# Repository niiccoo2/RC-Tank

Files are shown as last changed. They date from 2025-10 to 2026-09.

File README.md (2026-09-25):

Supported by [RTKdata](https://rtkdata.com/)

RTKdata logo



# Ships

_Wondering what a ship is? Watch [this](https://vimeo.com/1111478391) video! Basically, a ship is when you make your project experiancable by others. In this case, that is writing a README about the project and adding some videos so people can see what it is!_

### Version 4 BETA

This is a pretty small version, only 35 hours more than V3. This includes a bit of testing on the old frame, and then the start of designing the new frame. The new frame has been super fun to design but also super hard. Most of this is because all I knew was that I wanted a new frame, nothing else, but also because I didn't really know how to use Fusion. I will say that I learned a lot, and I am ready to finish up the frame. I'm hoping that this is over half of the new frame done, but it might end up taking a lot longer.

Features of new frame worked on for this ship:

- Main body
  - Figuring out how to connect all the aluminum was hard
- Start of the drivetrain

That doesn't sound like a lot, but it really is, especially when you don't know CAD.

CAD file for this ship can be found at `/CAD/V4/ships/V4b/V4b.step`.

**[Bill of materials](./BOM.md)** and **[wiring diagram](./WIRING.md)** — every part needed to build
V4 with quantities, prices and sources (~$2,613 total), and a diagram of how it all wires together.
Frame and drivetrain quantities come straight out of the V4b CAD.

Go look at the build journal (its pretty long! Scroll until you find V4, this ship was on SEP 5): [here!](./JOURNAL.md)

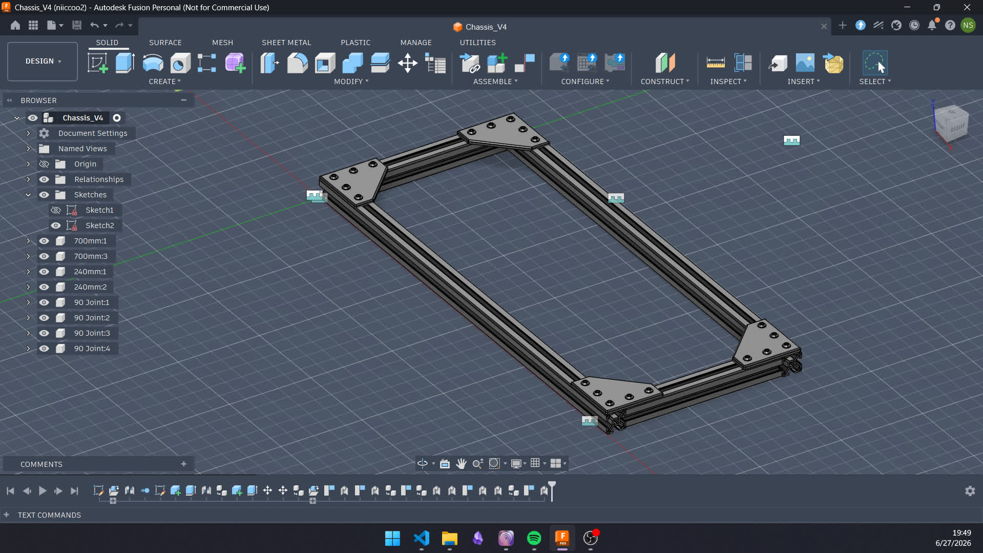
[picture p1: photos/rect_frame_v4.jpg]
Rectangle Frame V4

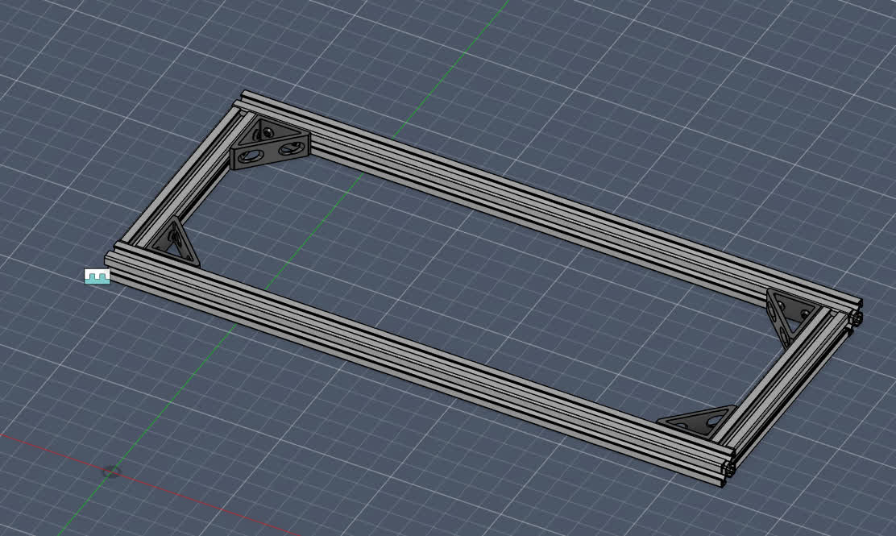
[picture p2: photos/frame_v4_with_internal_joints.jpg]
Chassis V4 with internal joints

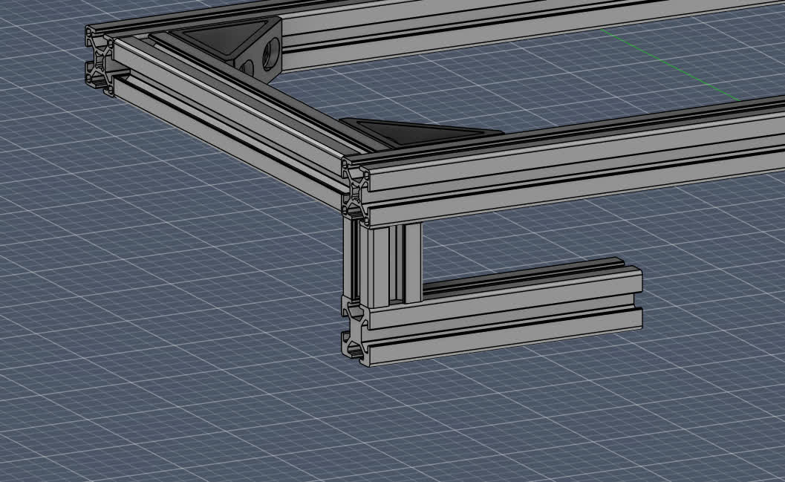
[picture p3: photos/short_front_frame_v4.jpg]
Short front on frame V4

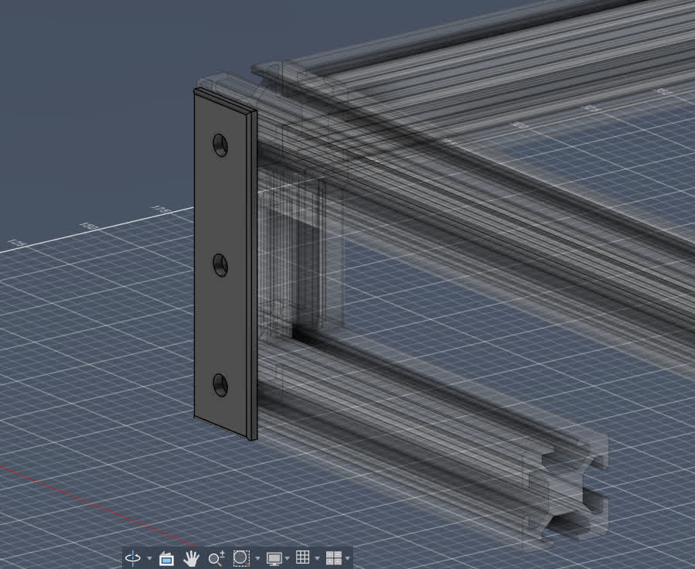
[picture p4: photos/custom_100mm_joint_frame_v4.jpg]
Custom 100mm joint

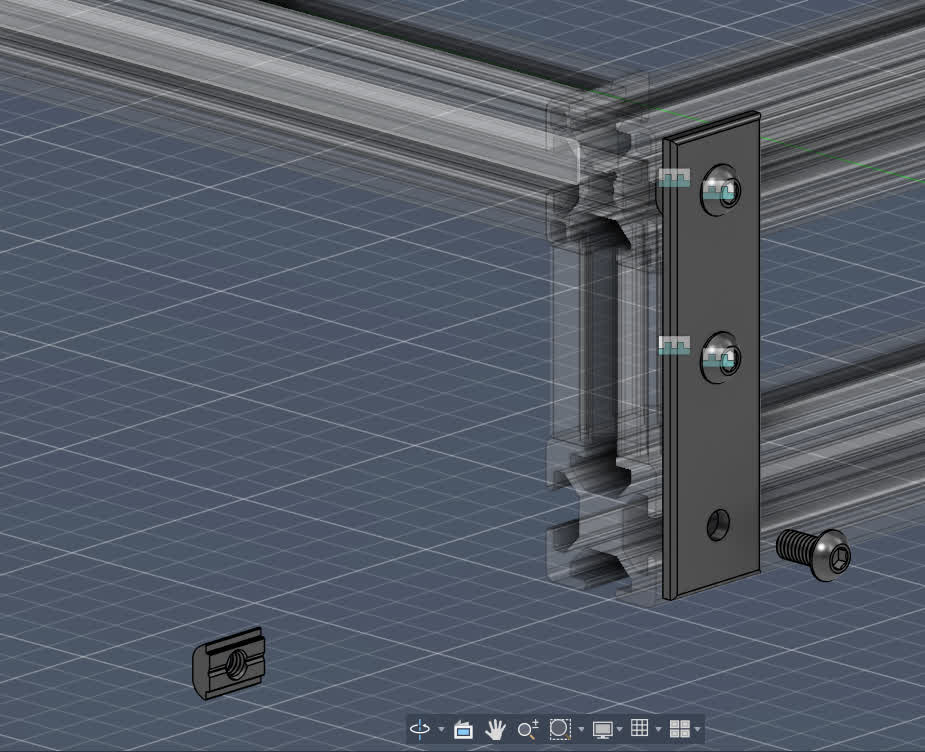
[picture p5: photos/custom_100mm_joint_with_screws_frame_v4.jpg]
Stupid screws

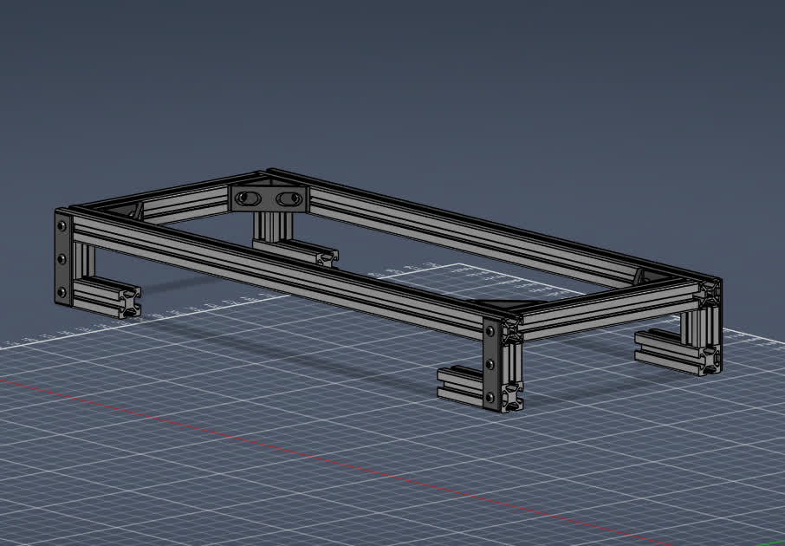
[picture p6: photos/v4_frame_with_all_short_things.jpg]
V4 frame with the short parts now on all sides

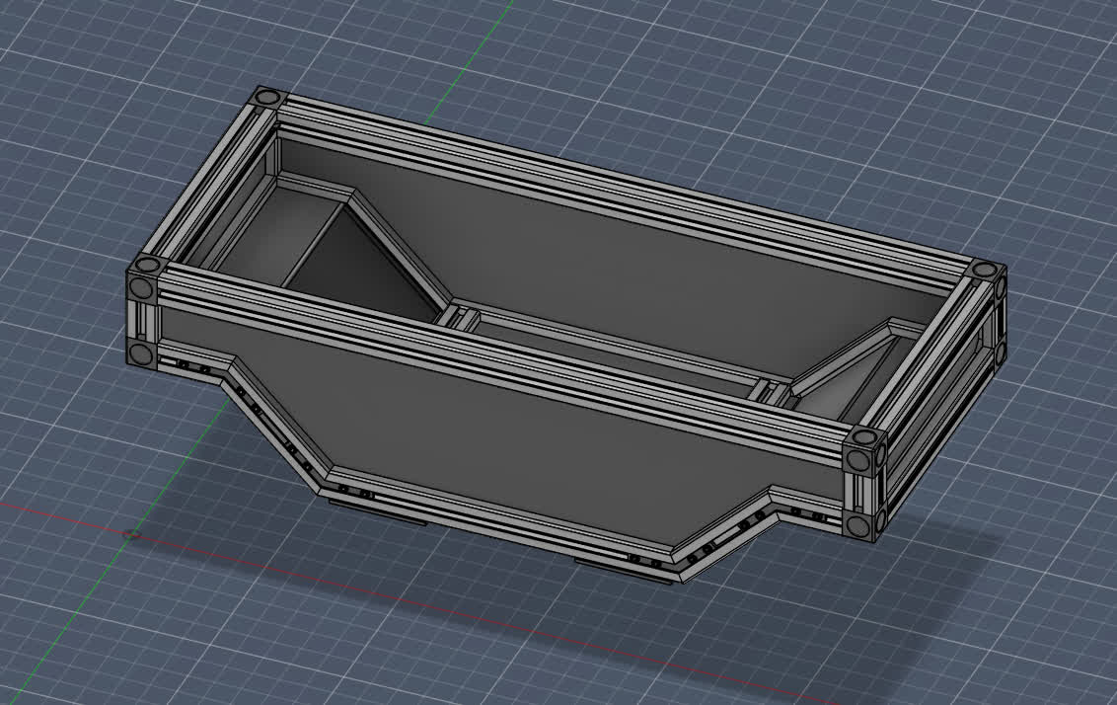
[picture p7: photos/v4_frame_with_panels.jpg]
The new frame with all the panels added

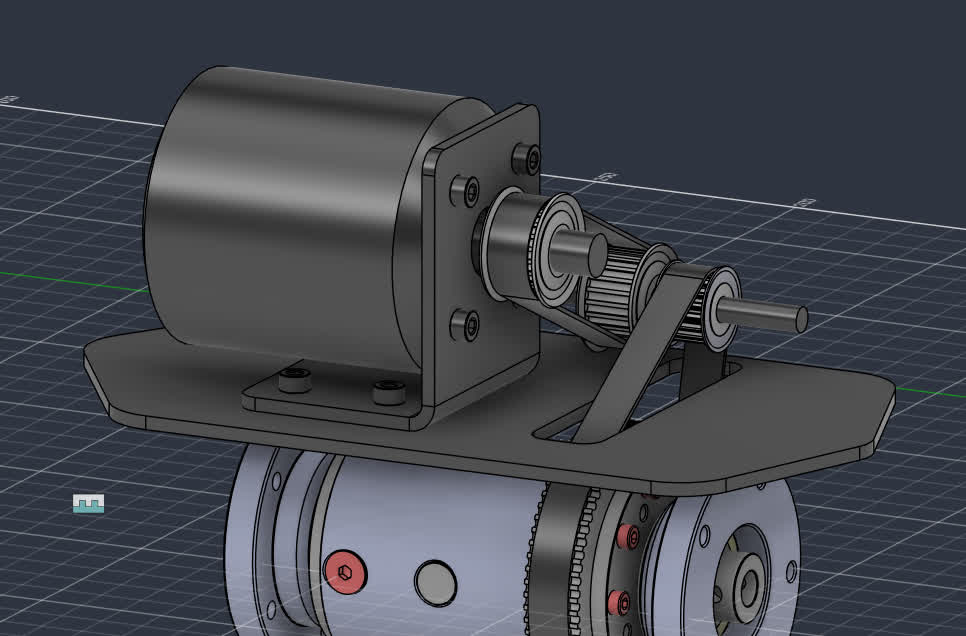
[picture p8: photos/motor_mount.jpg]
Motor mount in question

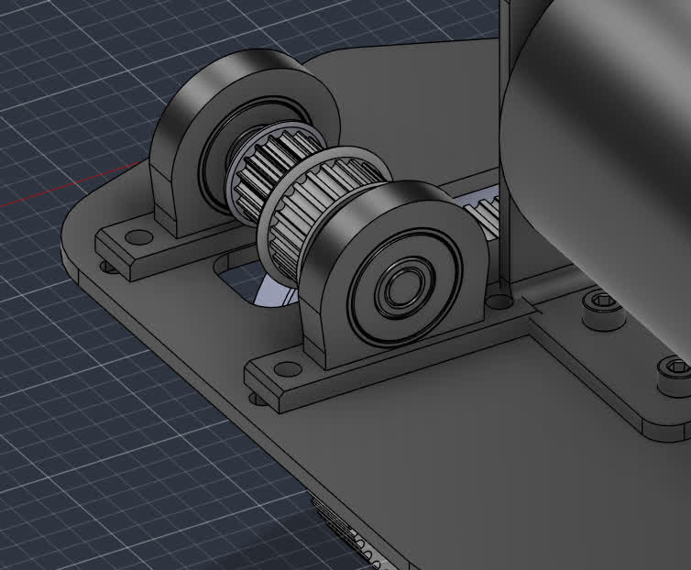
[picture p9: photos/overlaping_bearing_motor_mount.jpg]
The thing overlaping

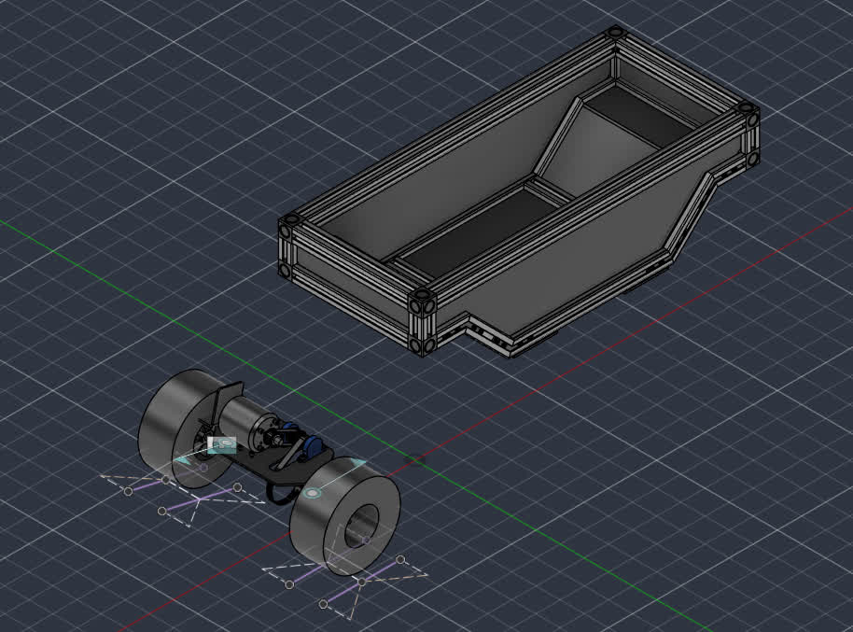
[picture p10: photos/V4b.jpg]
Final V4b


## Version 3

Features:

- Overall:
  - Low latency human driving using cellular
  - Waypoint driving using RTK GPS (under 30mm accuracy)
- Vehicle:
  - Hoverboard motors (very high tourque)
  - Neopixels for headlights and direction lights (red and green)
  - Camera for driving
  - GoPro monuts for videos (not needed to drive, only for extra video)
  - Handles because it weighs 35lbs (around 15kg)
  - Tech specs:
    - Nvidia Jetson Orin Nano
    - SIM7600 cell modem
    - SparkFun GPS-RTK2 Board
    - Hoverboard ECS's
    - 16Ah 4S LiPo battery
- Website:
  - Live video from tank (under 100ms control loop)
  - Live telemetry from tank:
    - Location
    - RTK GPS status
    - Battery voltage
    - Ping
    - Heading
  - Map:
    - View live location of tank
    - Create waypoint routes
    - Send routes to tank
    - Download and upload routes as JSON files
  - Tank settings:
    - Car mode (off lets you control each wheel by itself)
    - Lights
    - FrSky mode (for nicer controlers)
    - Self driving toggle
    - Video toggle
    - Refresh rate setting
  - Go check out the website at [rc.nicosmith.net](https://rc.nicosmith.net)! (Enter anything into text box and click connect)

Version 3 of this project has been based around adding waypoint following capabilities to the tank. There should also be version 3.5 coming out soon which will add ML features, such as staying on sidewalk and avoiding humans. This version has taken a while, but it is well worth it. The project as a whole has taken over 110 hours over 112 days (see, it really is a little bit every day). I redid the entire website UI, redid entire tank-side python software, and added waypoint following code. I have learned a lot about everything, from how much of a pain CSS can be, to how WebRTC doesn't follow system routing priorities, to how people are jerks and will steal stuff. Here are some awesome pictures and videos!

Go look at the build journal (its pretty long): [here!](./JOURNAL.md)

[Videos!](https://drive.proton.me/urls/YN5Q618FJM#a7Ycw6LDcv0I)

Tank in field
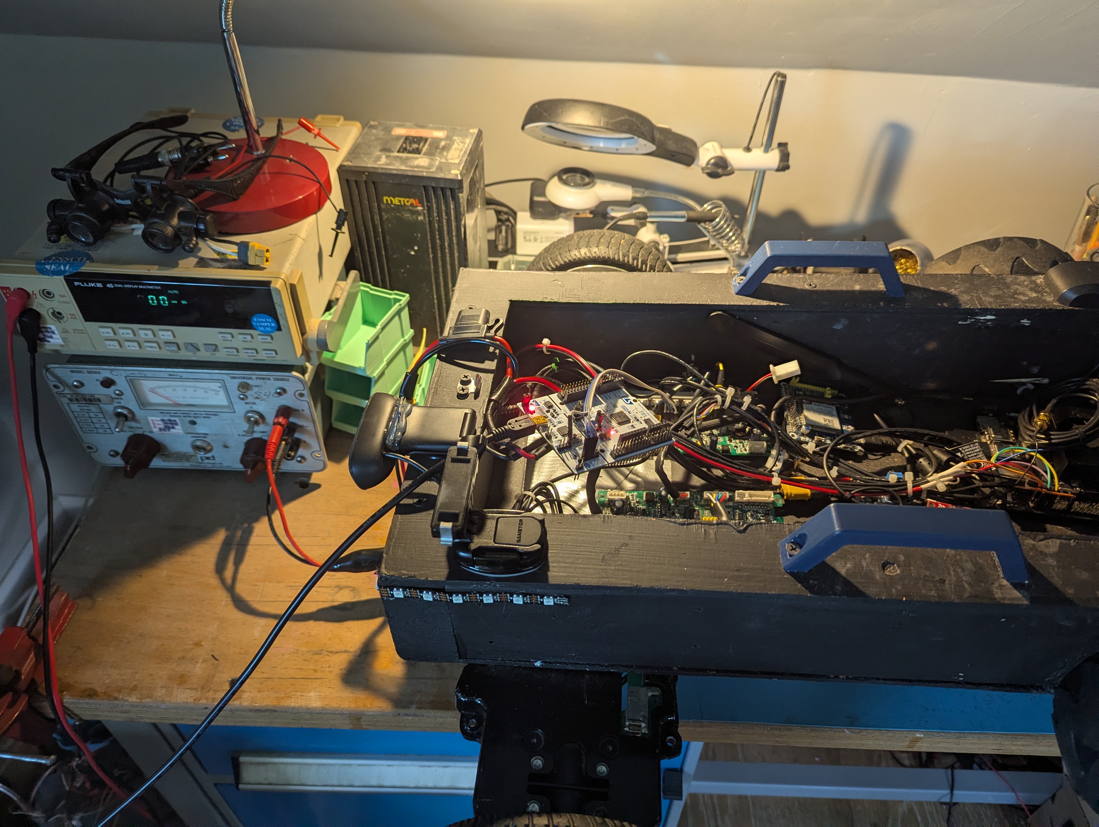
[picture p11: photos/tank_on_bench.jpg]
Tank on workbench

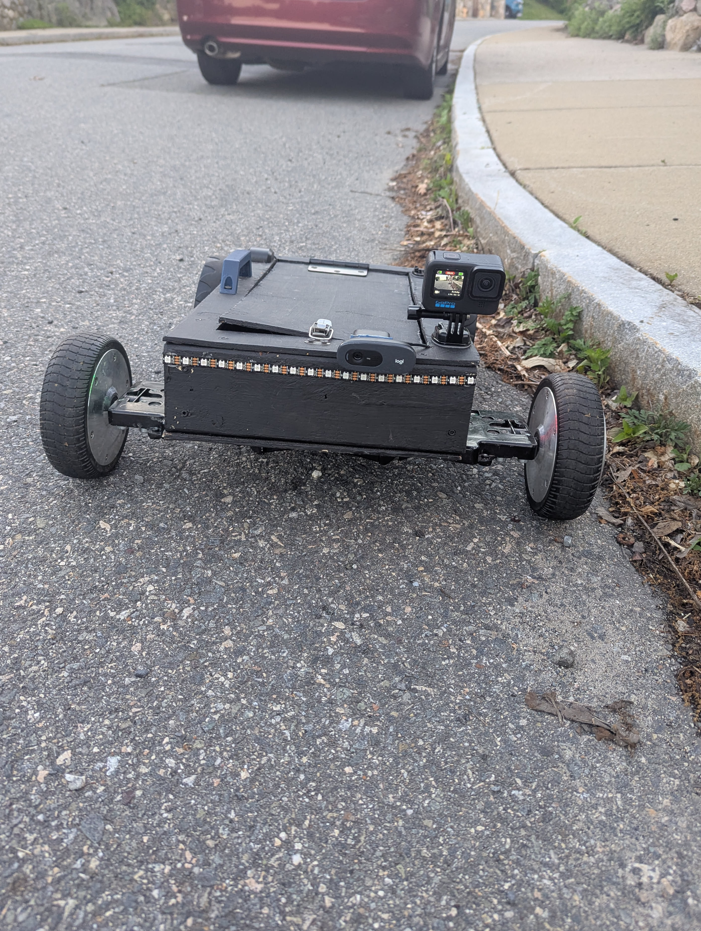
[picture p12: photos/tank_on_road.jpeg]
Tank on road

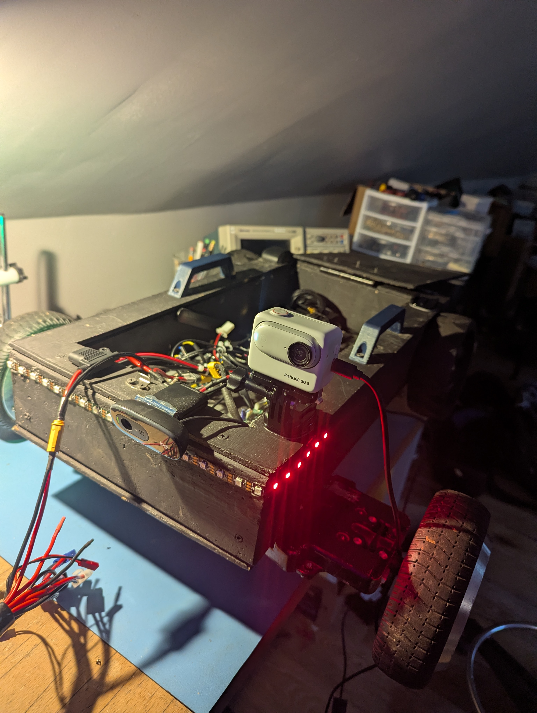
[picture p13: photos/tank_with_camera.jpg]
Tank with camera mounts

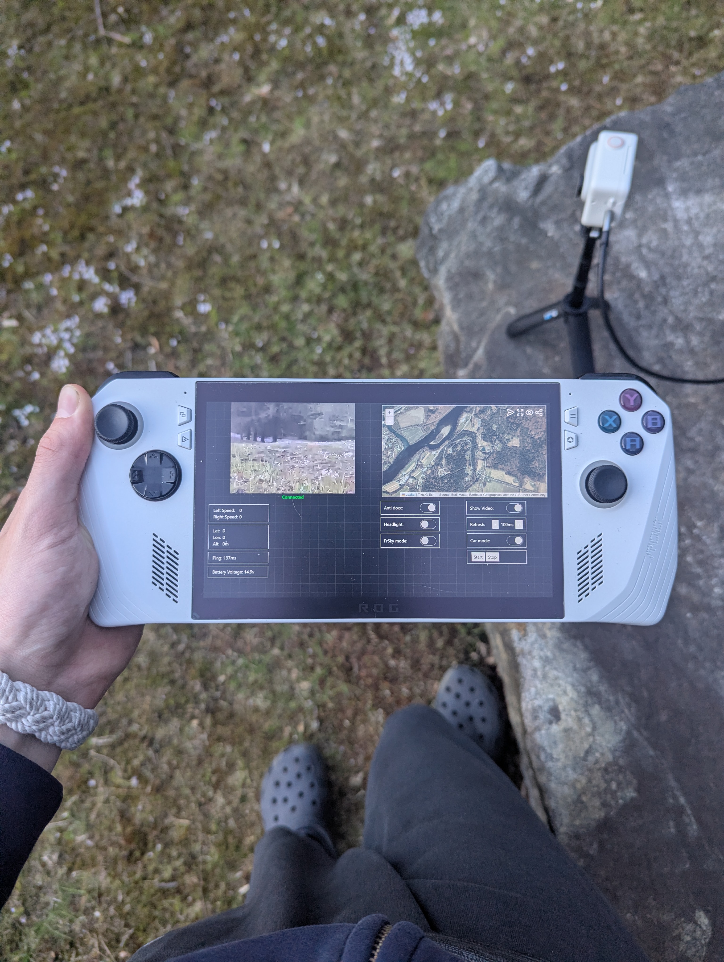
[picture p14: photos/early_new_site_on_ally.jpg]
Early version of new site on ally


## Versions 1 & 2

This is version 2 of my RC-Tank. It is no longer a tank but whatever. I created both versions 1 and 2 for Hack Club [Moonshot](https://moonshot.hackclub.com).

The idea of this project was simple, I had a normal rc car with camera, but it coulden't even go around the block, so I wanted something that would have much better range. Thats where using a cell modem comes in. The main (and big) disadvantage with this is latency, you need < 1.5s or else it becomes very hard to drive. I learned a lot doing this project (not done though!), I spent a lot of time learning about motor contollers and reverse engineering some hoverboard ECS's so I could use the motors I had. The main thing I want to keep working on, is the latency over cell, hopefully I can get webRTC working also. After I have a working human controled rover, then I will use it as the testbed for many more projects such as AI vision control, and GPS waypoints.

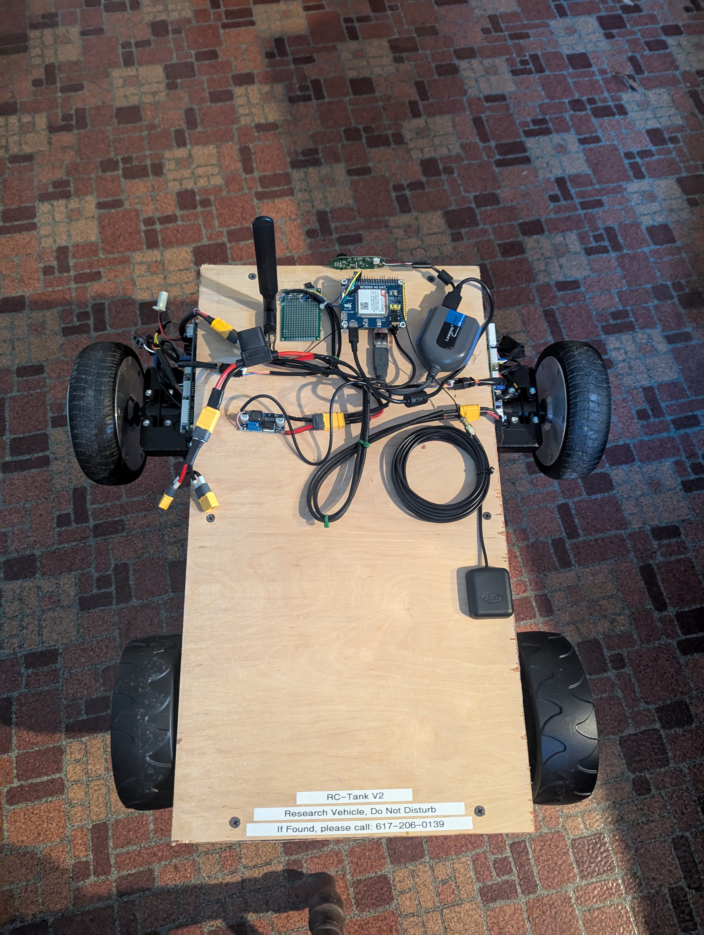
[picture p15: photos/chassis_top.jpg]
Top view of new frame


# Setup

## Internet

### Install Tailscale

Go to [login.tailscale.com/admin/machines](https://login.tailscale.com/admin/machines) and follow instructions for new linux device.

Use this command to start it so ssh will work: `sudo tailscale up --reset --netfilter-mode=off --ssh`.

### Turn off wifi power saving

```shell
sudo iw dev wlP1p1s0 set power_save off
```

You might need to use something like `ifconfig -a` to find the right network interface.

### Add networks and set wifi priority

```shell
sudo nmtui
```

```shell
sudo nmcli c mod "mypreferred" conn.autoconnect-priority 10
```

to set priority; higher number is higher priority.

### Cmd to temp use wifi

```shell
sudo ip route del default via 192.168.1.1 dev wlan0
sudo ip route add default via 192.168.1.1 dev wlan0 metric 50
```

### Cmd to dissconnect from WiFi

```shell
sudo ip link set wlan0 down

sudo ip link set wlan0 up

```

## Jetson specific

### Configure GPIO for SPI

To use SPI on the GPIO pins, you must first run the Jetson-IO python script and enable SPI1 (no idea why you need SPI1 for SPI0).

```shell
sudo /opt/nvidia/jetson-io/jetson-io.py
```

### Resize file system after copying from SD to SSD

```shell
sudo apt install cloud-utils
sudo growpart /dev/nvme0n1 1
sudo resize2fs /dev/nvme0n1p1
```

### Wiring

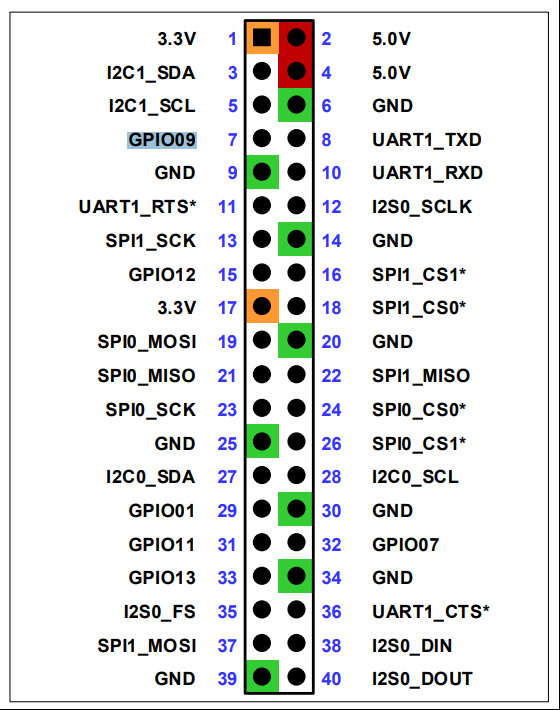
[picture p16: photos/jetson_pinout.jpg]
Jetson Pinout


(Wire color is to just help me)

| Pin # | Purpose  | Item | Wire Color |
| ----- | --- | --- | --- |
| 2 | 5V | Compass Power | Red |
| 3 | I2C1_SDA | Compass Data | Orange |
| 5 | I2C1_SCL | Compass Data | Brown |
| 6 | GND | ESC Serial Ground | Green |
| 8 | UART1_TX | ESC UART RX | Purple |
| 9 | GND | Compass Ground | Black |
| 10 | UART1_RX | ESC UART_TX | Yellow |
| 19 | SPI_0 | Lights Control | Orange |

## Website

You first need to directly go to one of the API endpoints to accept the self signed cert. _Remember that you have to use the :5000 port!_

## Custom TURN / STUN server

`sudo apt install coturn`

`sudo ufw allow 3478/udp`
`sudo ufw allow 3478/tcp`
`sudo ufw allow 50000:50050/udp`

Edit `/etc/turnserver.conf`

```conf
listening-port=3478
listening-ip=<YOUR_PUBLIC_IP>
external-ip=<YOUR_PUBLIC_IP>
realm=rc-tank
user=tank:tankpass
lt-cred-mech
fingerprint

min-port=50000
max-port=50050
```

`sudo systemctl restart coturn`
`sudo systemctl enable coturn`

Set the correct IP inside of `webrtc.py` and `webrtc.ts`

# Running the tank

`sudo JETSON_MODEL_NAME=JETSON_ORIN_NANO python3 ./main.py`

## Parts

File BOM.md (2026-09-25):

# Bill of Materials — V4

Everything needed to build **V4**. V4 is a new vehicle: new frame, new drivetrain, new motors, new
power system. The only things carried over are the compute and sensing stack (Jetson, RTK GPS,
compass, camera, modem, lights), which are listed in section 3.

Quantities for the frame and drivetrain are read straight out of the V4b CAD
(`/CAD/V4/ships/V4b/V4b.step`), so the cut lists and fastener counts are exact.

**Price key:** `~` means estimated. McMaster-Carr doesn't publish prices to search engines, so every
McMaster line is an estimate until I place the order. Prices are USD, no shipping or tax.

Wiring is in [WIRING.md](./WIRING.md).

---

## 1. Frame

All extrusion is **30 mm** T-slot (confirmed by the bracket the CAD uses — McMaster 3136N923 is the
"Flush 90 Degree Angle Bracket for 30mm High Rail"). Cut list from the CAD:

| Item | Qty | Price | Source |
| ---- | --- | ----- | --- |
| 30 mm T-slot extrusion — 700 mm | 2 | — | McMaster-Carr |
| 30 mm T-slot extrusion — 343 mm | 2 | — | McMaster-Carr |
| 30 mm T-slot extrusion — 240 mm | 6 | — | McMaster-Carr |
| 30 mm T-slot extrusion — 141 mm | 4 | — | McMaster-Carr |
| 30 mm T-slot extrusion — 100 mm | 4 | — | McMaster-Carr |
| 30 mm T-slot extrusion — 40 mm | 4 | — | McMaster-Carr |
| ↳ **4.65 m of extrusion**, bought as stock lengths and cut down | — | ~$150 | McMaster-Carr |
| 3-way 90° corner joint | 8 | ~$12 ea = ~$96 | McMaster [5537T864](https://www.mcmaster.com/5537T864/) |
| 45° structural bracket (sloped nose + tail) | 8 | ~$10 ea = ~$80 | McMaster [4844N18](https://www.mcmaster.com/4844N18/) |
| Flush 90° angle bracket, 30 mm rail | 4 | ~$8 ea = ~$32 | McMaster [3136N923](https://www.mcmaster.com/3136N923/) |
| T-slot nuts, screws and washers for all joints | ~120 | ~$50 | McMaster-Carr |
| Aluminum composite sheet, 24" × 60" × 1/8" black | 1 | $71.78 | [Home Depot — Falken ACM-BK-1/8-2460](https://www.homedepot.com/p/Falken-Design-24-in-x-60-in-x-1-8-in-Thick-Aluminum-Composite-ACM-Black-Sheet-Falken-Design-ACM-BK-1-8-2460/308670306) |
| ↳ cut by me into: left side, right side, front short, rear short, bottom | 5 panels | — | from sheet above |
| Front + rear bent panels — laser cut and bent | 2 | ~$90 | SendCutSend |
| Gasket / weatherstrip for the panel seams | 1 | ~$15 | Amazon |
| **Subtotal** | | **~$585** | |

The sheet is 9,120 cm² and the panels need ~3,280 cm², so one sheet covers it with room for mistakes.
Only the two bent panels go to SendCutSend — a plain rectangle was $36 there vs ~$5 of sheet cut at home.

## 2. Drivetrain

Beam axle. One motor per axle, belt down to an idler, second belt to a differential, then U-jointed
rods out to the wheels.

**The V4b CAD contains the front axle only.** The quantities below are for that one axle as modeled.
The full vehicle is 4WD, so double everything (the journal prices 2 diffs, not 1) — that's the
"×2 axles" column.

| Item | Qty / axle | ×2 axles | Price (both axles) | Source |
| ---- | --- | --- | --- | --- |
| Flipsky 6384 190 KV sensored BLDC motor | 1 | 2 | ~$119 ea = ~$238 | [Flipsky](https://flipsky.net/collections/hobby-motors-for-esk8-ebike-efoil) |
| Flipsky VESC (motor controller) | 1 | 2 | ~$80 ea = ~$160 | Flipsky |
| Differential — gears, cross pins, 10×0.2 shims | 1 | 2 | <$100 total | AliExpress, built to [this GrabCAD diff](https://grabcad.com/library/differential-for-rc-quarterscale-cars) scaled up |
| 3D printed diff housing + mounts (PETG) | 1 set | 2 | ~$10 filament | Self-printed |
| HTD 3M 24-tooth pulley, 6 mm bore | 2 | 4 | ~$8 ea = ~$32 | AliExpress |
| HTD 3M belt, 174 mm (motor → idler) | 1 | 2 | ~$6 ea = ~$12 | AliExpress |
| HTD 3M belt (idler → diff) | 1 | 2 | ~$6 ea = ~$12 | AliExpress |
| 440C stainless ball bearing (idler) | 2 | 4 | ~$6 ea = ~$24 | McMaster [4668K235](https://www.mcmaster.com/4668K235/) |
| Idler pulley bearing, p/n 17021800 | 2 | 4 | ~$5 ea = ~$20 | AliExpress |
| 6 mm jack rod (idler shaft) | 1 | 2 | ~$5 ea = ~$10 | McMaster-Carr |
| 8 mm U-joint | 2 | 4 | ~$12 ea = ~$48 | AliExpress |
| 8 mm steel rod — 25 / 34 / 34 / 41 mm cuts | 4 | 8 | ~$15 total | McMaster-Carr |
| 8 mm rod → 12 mm hex wheel adapter | 2 | 4 | ~$10 ea = ~$40 | AliExpress |
| Wheel + tire, 1/5 scale | 2 | 4 | ~$25 ea = ~$100 | AliExpress |
| Mounting plate, motor mount, 2× idler bearing mount — 1/8" (3.2 mm) bent sheet | 1 set | 2 | ~$45 ea = ~$90 | SendCutSend |
| M5 socket head screw, motor to mount | 4 | 8 | ~$10 | McMaster [91292A116](https://www.mcmaster.com/91292A116/) |
| M5 socket head screw, motor mount + idler bolts | 7 | 14 | ~$14 | McMaster [91292A117](https://www.mcmaster.com/91292A117/) |
| Steel hex nut, motor mount | 4 | 8 | ~$5 | McMaster [90592A011](https://www.mcmaster.com/90592A011/) |
| Steel hex nut, idler bolts | 3 | 6 | ~$4 | McMaster [90592A090](https://www.mcmaster.com/90592A090/) |
| Black coated steel washer, motor mount | 4 | 8 | ~$5 | McMaster [93413A211](https://www.mcmaster.com/93413A211/) |
| **Subtotal (both axles)** | | | **~$944** | |

## 3. Power and electronics

The Jetson, GPS, compass, camera, modem and lights move over from V3 unchanged — everything below
the double line is new for V4.

| Item | Qty | Price | Source |
| ---- | --- | ----- | --- |
| 6S LiPo pack — 2 in series gives 12S / 44.4 V | 2 | ~$130 ea = ~$260 | Hobby shop |
| Anti-spark switch + inline fuse (12S) | 1 | ~$25 | Amazon |
| Buck converter, 44.4 V → 5 V | 1 | ~$15 | Amazon |
| XT90 connectors, 10 AWG silicone wire, heat shrink | lot | ~$30 | Amazon |
| — *carried over from V3* — | | | |
| NVIDIA Jetson Orin Nano Super Dev Kit | 1 | $249 paid (now $399) | [NVIDIA](https://www.nvidia.com/en-us/autonomous-machines/embedded-systems/jetson-orin/nano-super-developer-kit/) |
| 512 GB NVMe SSD (boot drive) | 1 | ~$40 | Amazon |
| SparkFun GPS-RTK2 — ZED-F9P (Qwiic) | 1 | $259.95 | [SparkFun GPS-15136](https://www.sparkfun.com/sparkfun-gps-rtk2-board-zed-f9p-qwiic-gps-15136.html) |
| GNSS L1/L2 antenna + SMA cable | 1 | ~$70 | SparkFun |
| Waveshare SIM7600G-H 4G USB dongle + antenna | 1 | ~$70 | [Waveshare](https://www.waveshare.com/sim7600g-h-4g-dongle.htm) |
| LTE SIM + data plan | 1 | ~$10/mo | Carrier |
| Adafruit QMC5883P magnetometer (compass) | 1 | ~$5 | Adafruit |
| USB webcam (driving camera) | 1 | ~$30 | Amazon |
| Powered USB hub | 1 | ~$20 | Amazon |
| WS2812B NeoPixel strip, 30 px | 1 | ~$10 | Amazon |
| **Subtotal** | | **~$1,084** | |

## Totals

| Section | Cost |
| --- | ---- |
| Frame | ~$585 |
| Drivetrain (both axles) | ~$944 |
| Power and electronics | ~$1,084 |
| **Total** | **~$2,613** |

## Not in the V4 build

V1–V3 drove on two hoverboard hub motors and the two GD32 ESC boards out of a salvaged hoverboard,
running [RoboDurden's firmware](https://github.com/RoboDurden/Hoverboard-Firmware-Hack-Gen2.x-GD32).
All of that is replaced in V4 by the Flipsky motors, VESCs and the belt-and-diff drivetrain above.

Tools used but not consumed: 3D printer + PETG, soldering iron, hand tools, drill, calipers, logic
analyzer, ST-Link V2, and Fusion 360 (free hobbyist licence).

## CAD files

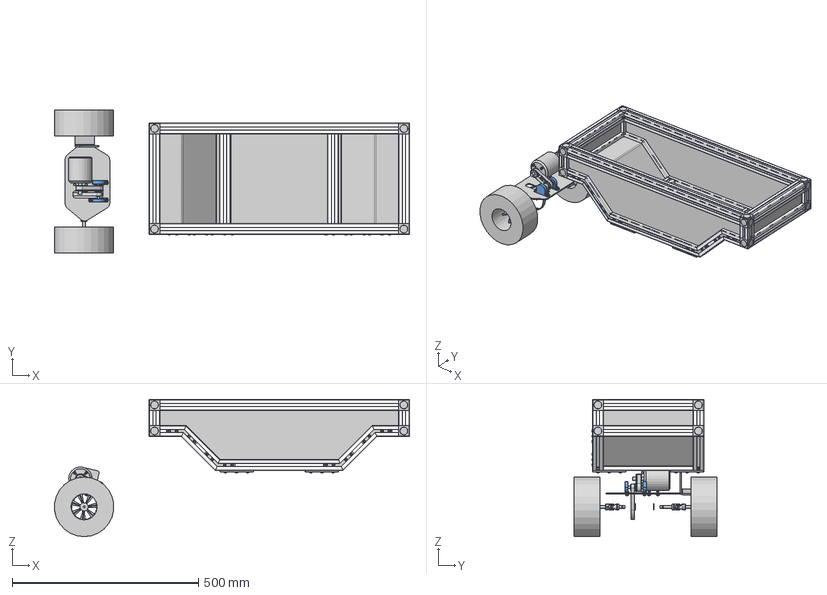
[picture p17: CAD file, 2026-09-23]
CAD/V4/ships/V4b/V4b.step
954.0 x 383.5 x 368.8 mm
4844N18_T-Slotted Framing Structural Bracket x 8
5537T864_T-Slotted Framing x 8
3136N923_Flush 90 Degree Angle Bracket for 30mm High Rail T-Slotted F raming x 4
90592A011_Low-Strength Steel Hex Nuts
93413A211_Black Super-Corrosion-Resistant-Coated Steel Washer
91292A117_18-8 Stainless Steel Socket Head Screw
4668K235_Permanently Lubricated 440C Stainless Steel Ball Bearing x 2
91292A117_18-8 Stainless Steel Socket Head Screw_1 x 2
90592A090_Steel Hex Nut x 2

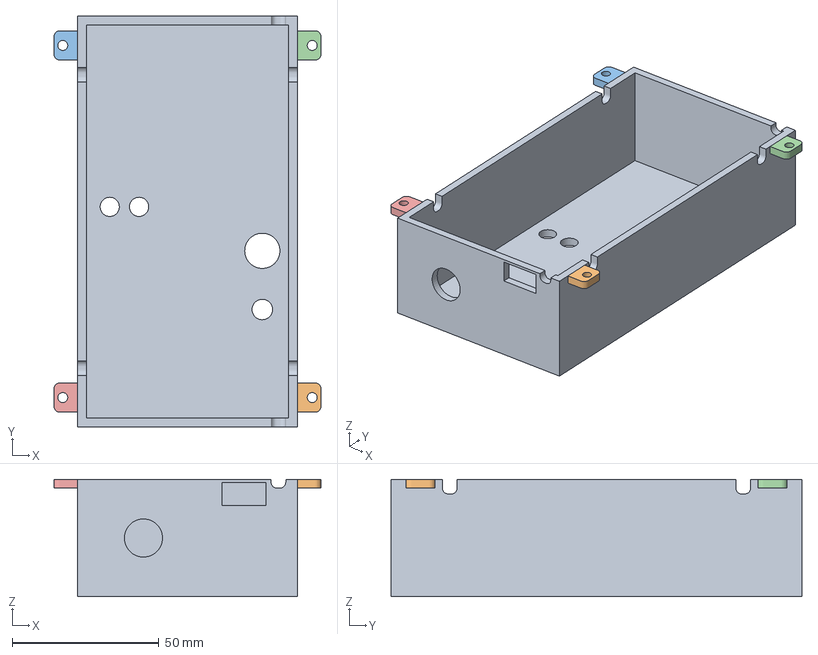
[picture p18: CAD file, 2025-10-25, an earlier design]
CAD/V0.5/cover/Cover_V3.3mf
91.0 x 140.0 x 40.0 mm

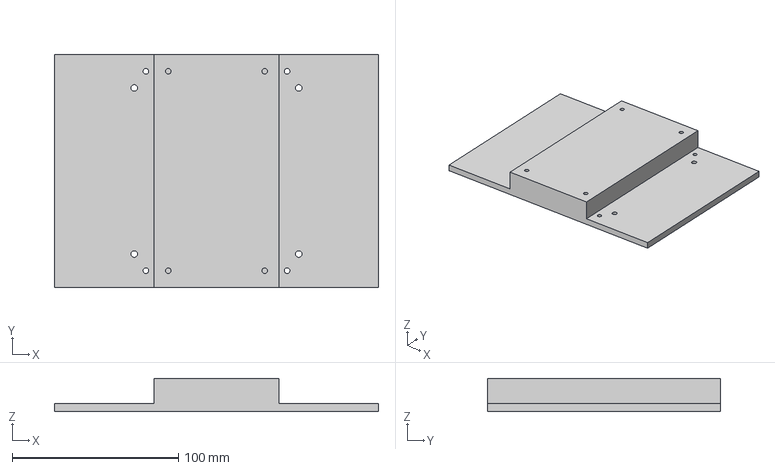
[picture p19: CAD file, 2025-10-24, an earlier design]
CAD/V0.5/riser/Platform_Riser_V4.3mf
195.0 x 140.0 x 20.0 mm

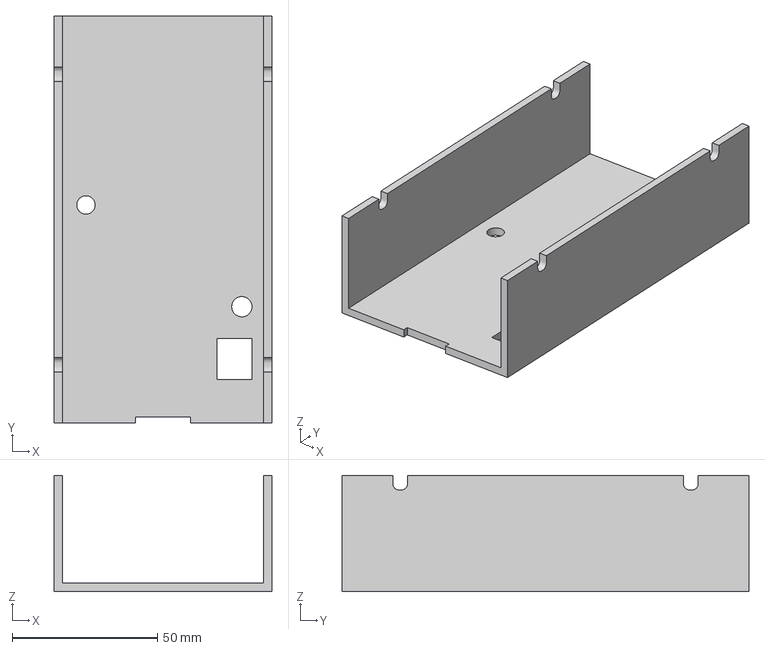
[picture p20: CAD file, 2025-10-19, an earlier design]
CAD/V0.5/cover/Cover_V2.3mf
75.0 x 140.0 x 40.0 mm

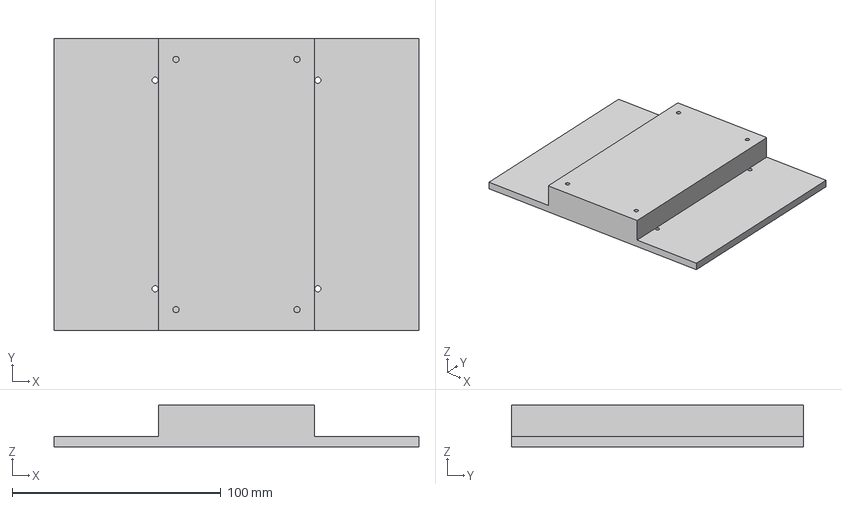
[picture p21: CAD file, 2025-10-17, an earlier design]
CAD/V0.5/riser/Platform_Riser_V3.3mf
175.0 x 140.0 x 20.0 mm

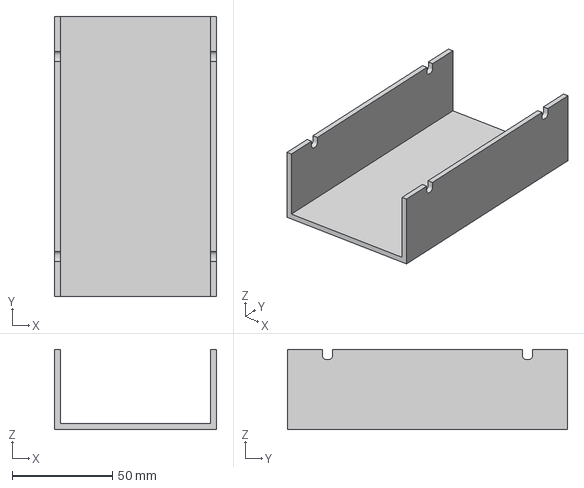
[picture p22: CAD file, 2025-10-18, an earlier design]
CAD/V0.5/cover/Cover.3mf
81.0 x 140.0 x 40.0 mm

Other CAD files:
CAD/V0.5/riser/Platform_Riser_V2.3mf
CAD/V0.5/riser/Platform_Riser.3mf
CAD/V0.5/cover/Cover.f3d
CAD/V0.5/cover/Cover_V2.f3d
CAD/V0.5/cover/Cover_V3.f3d
CAD/V0.5/riser/Platform_Riser.f3d
CAD/V0.5/riser/Platform_Riser_V2.f3d
CAD/V0.5/riser/Platform_Riser_V3.f3d
CAD/V0.5/riser/Platform_Riser_V4.f3d
CAD/V4/Chassis_V4_Rect_Internal_Joints.f3d
CAD/V4/Chassis_V4_Short_On_All_Sides.f3d
CAD/V4/Chassis_V4_Start_On_Front.f3d
CAD/V4/Chassis_V4_with_panels.f3d
CAD/V4/ships/V4b/V4b.3mf

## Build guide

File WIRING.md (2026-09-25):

# Wiring Diagram — V4

How everything in the [BOM](./BOM.md) wires together on **V4**. V4 runs a 12S pack into two VESCs
driving two Flipsky BLDC motors — one per beam axle, belted to a differential. The compute and
sensing side (Jetson, RTK GPS, compass, camera, modem, lights) carries over from V3 unchanged.

Arrows with a voltage are power. Arrows with a protocol are data.

```mermaid
flowchart LR
    subgraph PACK["12S pack"]
        B1["6S LiPo<br>22.2 V"]
        B2["6S LiPo<br>22.2 V"]
    end

    subgraph FRONT["Front axle"]
        VF["Flipsky VESC<br>front"]
        MF["Flipsky 6384<br>190 KV sensored"]
        DF["Belt to idler,<br>belt to diff,<br>U-joints to 2 wheels"]
    end

    subgraph REAR["Rear axle"]
        VR["Flipsky VESC<br>rear"]
        MR["Flipsky 6384<br>190 KV sensored"]
        DR["Belt to idler,<br>belt to diff,<br>U-joints to 2 wheels"]
    end

    B1 -->|series| B2
    B2 -->|44.4 V| FUSE["Fuse +<br>anti-spark switch"]
    FUSE --> BUS["Power bus"]
    BUS -->|44.4 V| VF
    BUS -->|44.4 V| VR
    BUS -->|44.4 V| BUCK["Buck converter<br>44.4 V to 5 V"]

    BUCK -->|5 V| JET
    BUCK -->|5 V| HUB
    BUCK -->|5 V| LED

    VF -->|"3-phase + hall sensor cable"| MF
    VR -->|"3-phase + hall sensor cable"| MR
    MF -->|belts and diff| DF
    MR -->|belts and diff| DR

    JET["Jetson Orin Nano<br>40-pin header"]

    JET -->|"UART1 - pin 8 TX / pin 10 RX / pin 6 GND"| VF
    VF -->|"CAN bus"| VR
    JET -->|"I2C1 - pin 3 SDA / pin 5 SCL<br>pin 2 = 5 V, pin 9 = GND"| CMP["QMC5883P compass"]
    JET -->|"SPI0 - pin 19, 6.4 MHz"| LED["30x WS2812B NeoPixels<br>head / tail / turn"]
    JET -->|USB| HUB["Powered USB hub"]

    HUB -->|USB| CAM["USB camera"]
    HUB -->|"USB - AT / PPP"| MDM["SIM7600G-H 4G modem"]
    HUB -->|"USB - /dev/ttyACM0, 38400"| GPS["SparkFun ZED-F9P<br>RTK GPS"]

    GPS -->|SMA| ANT["GNSS L1/L2 antenna"]
    MDM -->|SMA| LTE["LTE antenna"]

    MDM -->|"internet - RTCM3 in / WebRTC + WS out"| NET(["NTRIP caster<br>+ website"])
```

## Notes

- **The 5 V rail needs its own converter.** The stack pulls ~3.2 A at 5 V (Jetson ~1 A, modem ~2 A,
  camera ~200 mA). On V3 I tried to run it off the ESC BECs, which only gave 1 A each, and it caused
  a long run of bugs that all looked like software problems. Don't repeat that.
- **12S needs an anti-spark switch,** not a bare switch — 44.4 V into the VESC caps will weld a
  plain contact.
- **One VESC is the master.** The Jetson talks UART to the front VESC only; the front VESC forwards
  to the rear over CAN. Same idea as the V3 UART bus, one link from the host instead of two.
- **Motors are sensored,** so each one needs the hall sensor cable back to its VESC as well as the
  three phase wires. Without it low-speed torque is bad, which matters for a heavy rover.
- **SPI must be enabled first** or the lights silently do nothing: run
  `sudo /opt/nvidia/jetson-io/jetson-io.py` and enable SPI1 (yes, SPI1 — it shows up as
  `/dev/spidev0.0`).
- **The compass needs its ground.** It reads garbage rather than erroring if pin 9 is missing.
- **Antennas go outside the shell.** The frame is aluminium, so the GNSS and LTE antennas need SMA
  bulkheads through the top panel.

## Jetson pin assignments

Unchanged from V3, except pins 6/8/10 now go to the front VESC instead of the hoverboard ESC.

| Pin # | Purpose  | Item | Wire Color |
| ----- | --- | --- | --- |
| 2 | 5V | Compass Power | Red |
| 3 | I2C1_SDA | Compass Data | Orange |
| 5 | I2C1_SCL | Compass Data | Brown |
| 6 | GND | VESC Serial Ground | Green |
| 8 | UART1_TX | VESC UART RX | Purple |
| 9 | GND | Compass Ground | Black |
| 10 | UART1_RX | VESC UART TX | Yellow |
| 19 | SPI_0 | Lights Control | Orange |

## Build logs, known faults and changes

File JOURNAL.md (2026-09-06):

# Journal

## **VERSION 1**

I did not count the time building the chassis kit.

### Thursday, October 16th | 30 minutes

Spent 30 minutes designing a simple riser so that I can fit more stuff on the tank. There is not enough room otherwise. This is mainly so I can start installing everything tmrw, once I have an idea of where things fit, I'll make a better version.
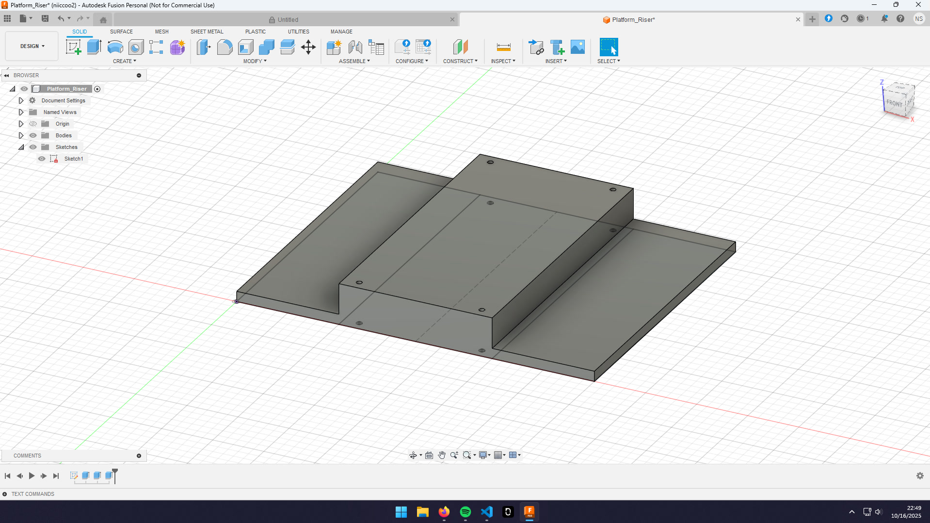
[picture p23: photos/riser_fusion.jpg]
Fusion

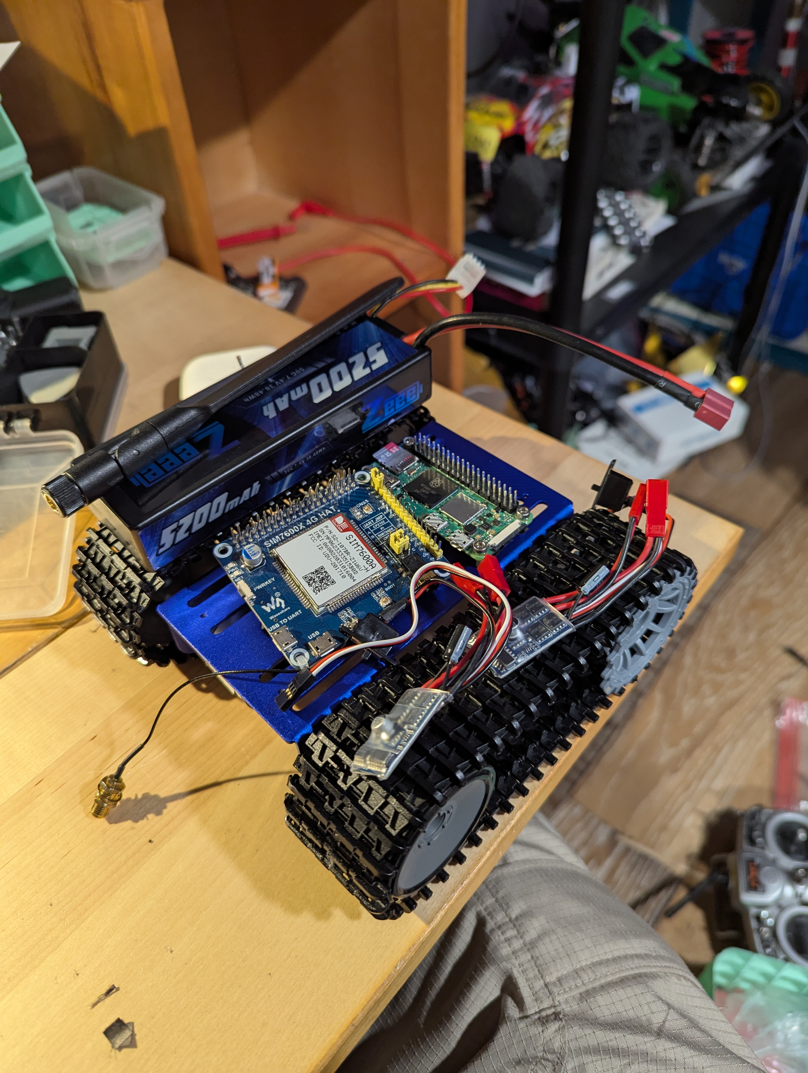
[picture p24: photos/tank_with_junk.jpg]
Wayyy too much stuff on the tank

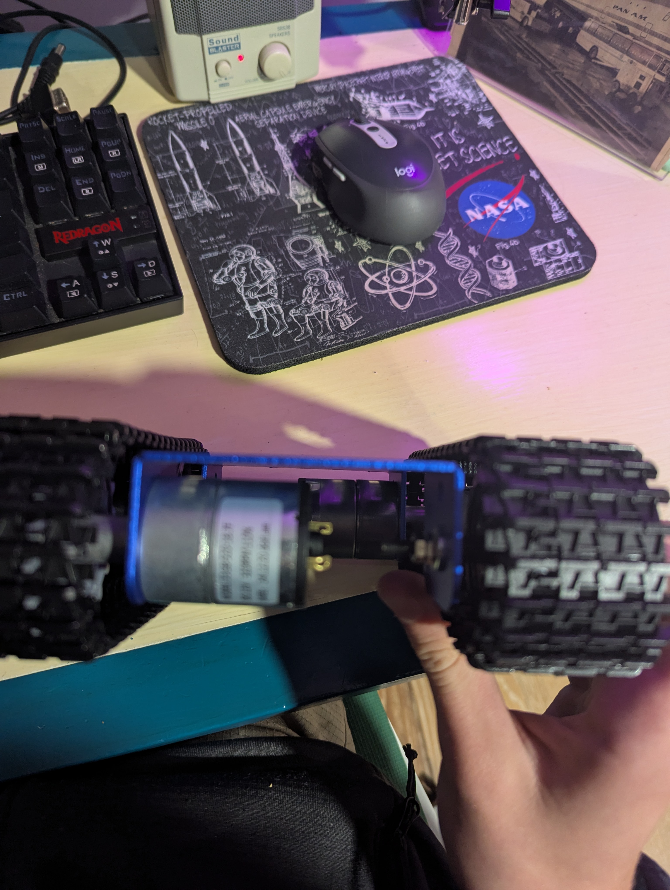
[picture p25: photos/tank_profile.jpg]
Profile of tank


### Friday, October 17th | 4 hours

#### 07:00 | 30 minutes

Tested V1 of the riser. It covered the tracks fine, but I made the screw holes too small and mismeasured where the holes in the chassis are. I spent 30 making V2 with the following improvements.

- Fix size of screw holes
- Fix chassis mountiung hole locations
- Add holes for mounting RPI Zero
- Add holes to ziptie batterys on the edge
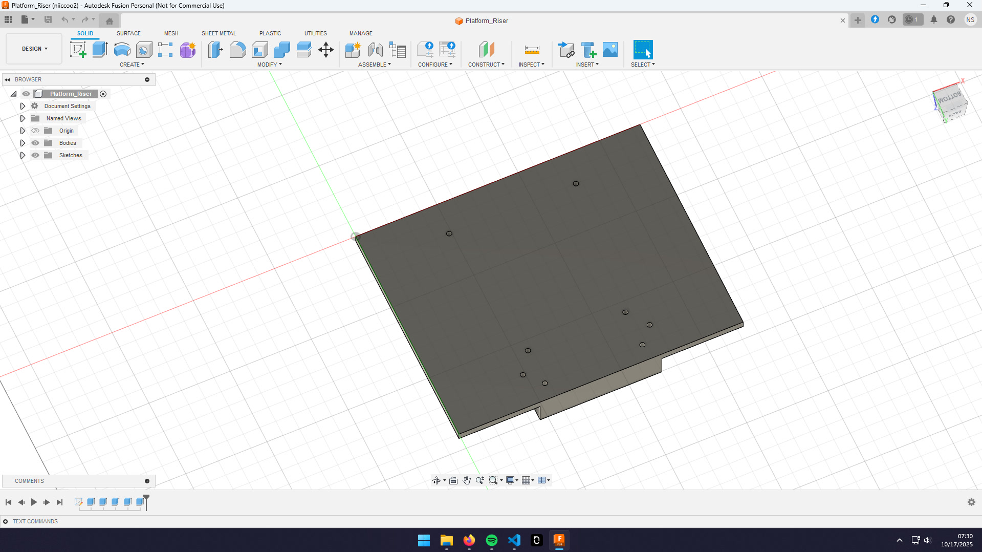
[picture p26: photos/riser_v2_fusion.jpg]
V2 of the riser in fusion
  
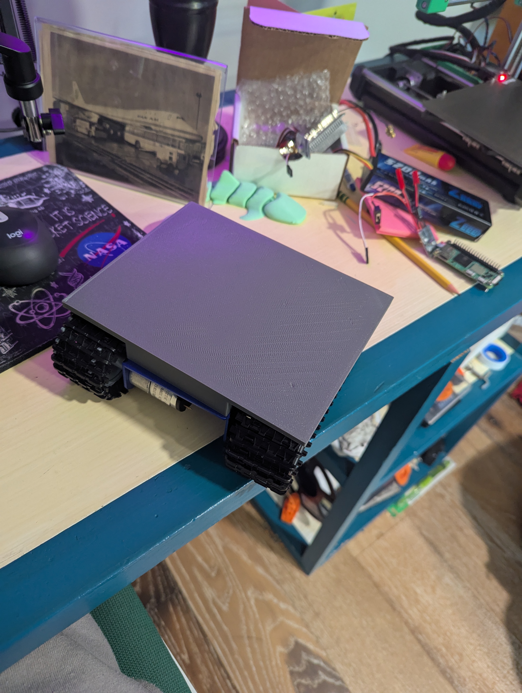
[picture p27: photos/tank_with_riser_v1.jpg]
Tank with V1 of riser
  

#### 16:00 | 30 minutes

Took apart the car and tracks to test V2 of the riser. The mounting holes distance to edge rn is good but apparently I misread the design sheet and made them to far apart. So I made a quick edit and started V3 on the printer.
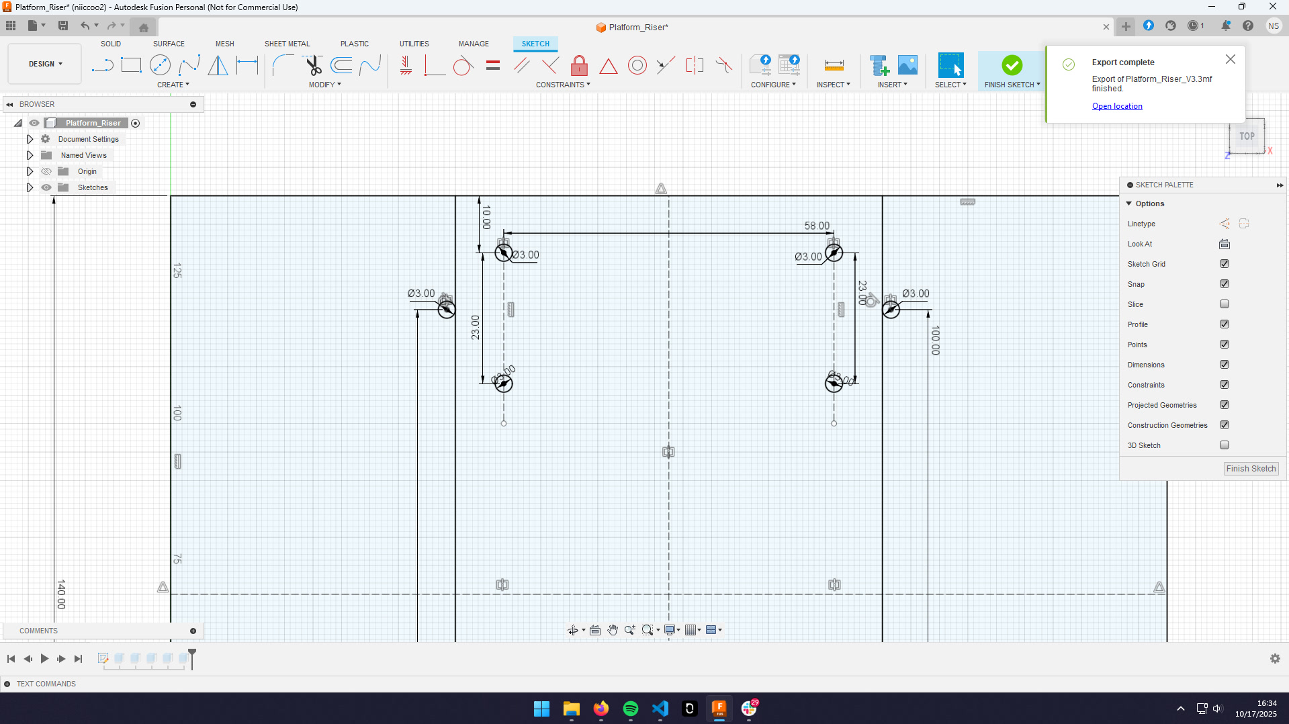
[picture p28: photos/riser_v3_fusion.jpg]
V3 of riser in fusion


#### 18:30 | 1 hour

Soldered a bunch of cables to the motor controllers and did first boot of pi from the tank battery. V3 of the riser is almost done printing. Going to start researching and writing code to make the motors spin!
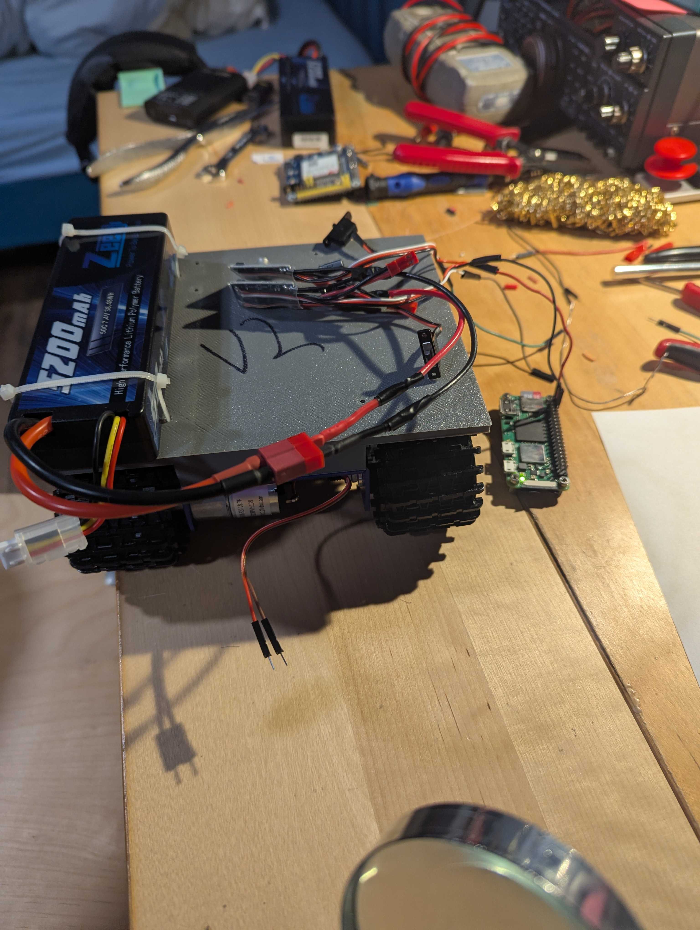
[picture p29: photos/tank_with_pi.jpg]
Tank with pi on it


#### 20:00 | 2 hours

Got the car to drive. But one of the free wheels is locking up, v3 of the riser but finished printing so I'll fix the wheel as I put the new version on. Put V3 of riser on tank. ALL SCREWS LINE UP!!

### Saturday, October 18th | 3.25 hours

#### 10:00 | 1 hour

Added a lcd screen that displays the IP because it kept changing ip. Also wrote code so that it auto displays on boot. Right now its seprate from main.py but at some point I will find a way to intigrate once I feel safe having it auto run main.py.
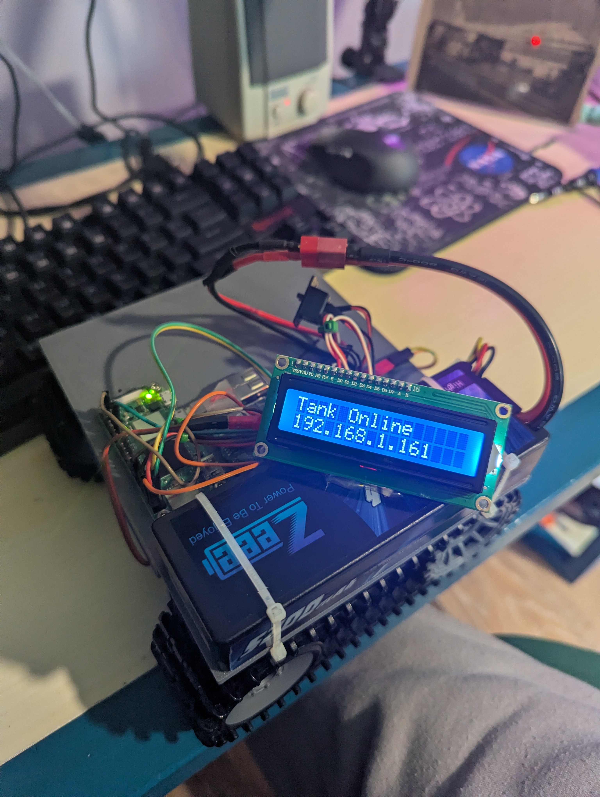
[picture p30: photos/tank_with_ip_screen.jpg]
Tank with screen showing the IP


#### 14:30 | 15 minutes

Seeing how quickly I'm running out of room, I designed a cover for the pi, modem and camera so that I could mount more stuff like the screen, antennas, lights, and other goodies.
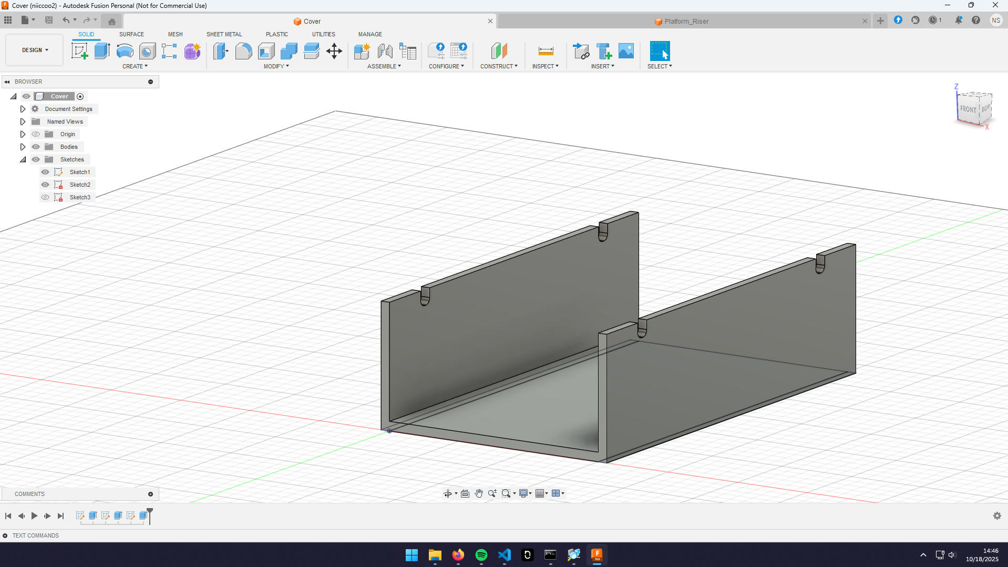
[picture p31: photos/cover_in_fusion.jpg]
Cover in fusion


#### 20:25 | 30 minutes

Tested the cover and made some changes and printed v2. Still going to use hot glue to mount until I redo the riser.
Changes:

- Make total width 75mm instead of 3+75+3
- Add hole for power switches
- Add hole for SMA connector
- Add hole for LCD cables
- Add notch for camera
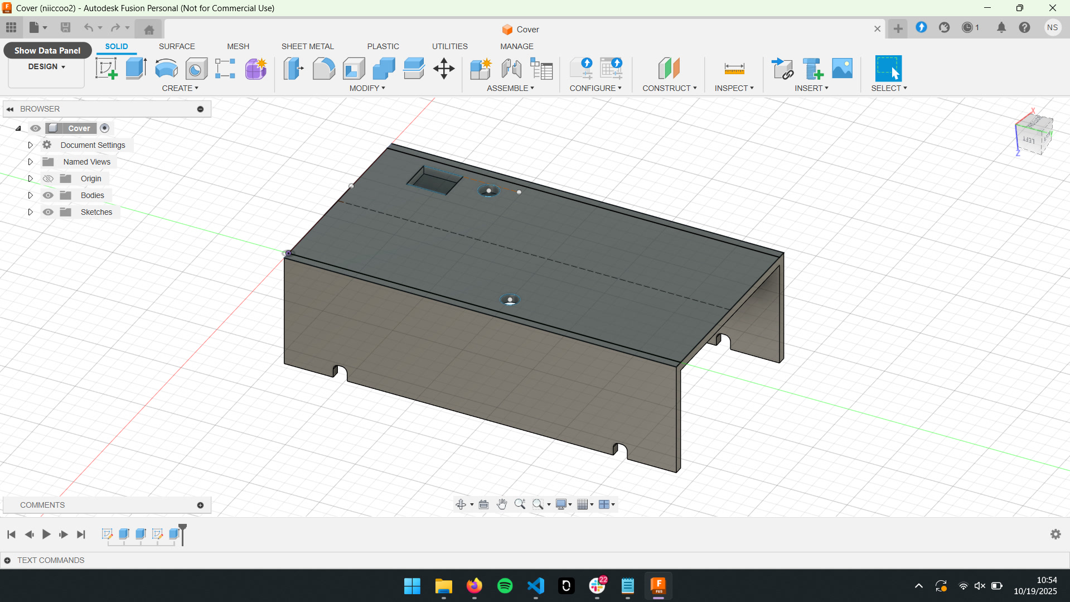
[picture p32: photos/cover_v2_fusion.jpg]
Cover V2 in fusion
  

#### 21:40 | Not logging this time

Just spent 20 minutes figuring out why code was not working, but it was because I was never pulling changes to the tank... Also forgot that a vertical cam makes a vertical stream so going to put it back into original positon and remove the notch in the cover for it. Not a big deal so not printing V3 of cover yet.

#### 22:00 | 1.5 hours

Worked on the website and debugged the twitches. I want to make the website look nicer but I'm going to get some more features working first.
Website changes:

- Embed video stream
- Add connection status
- Add var to enable or disable cam (Added, but did not add a ui switch yet)
- Add ping
- Redo layout

### Sunday, October 19th | 2 hours

#### 08:00 | 30 minutes

Installed the modem and V2 of the cover.
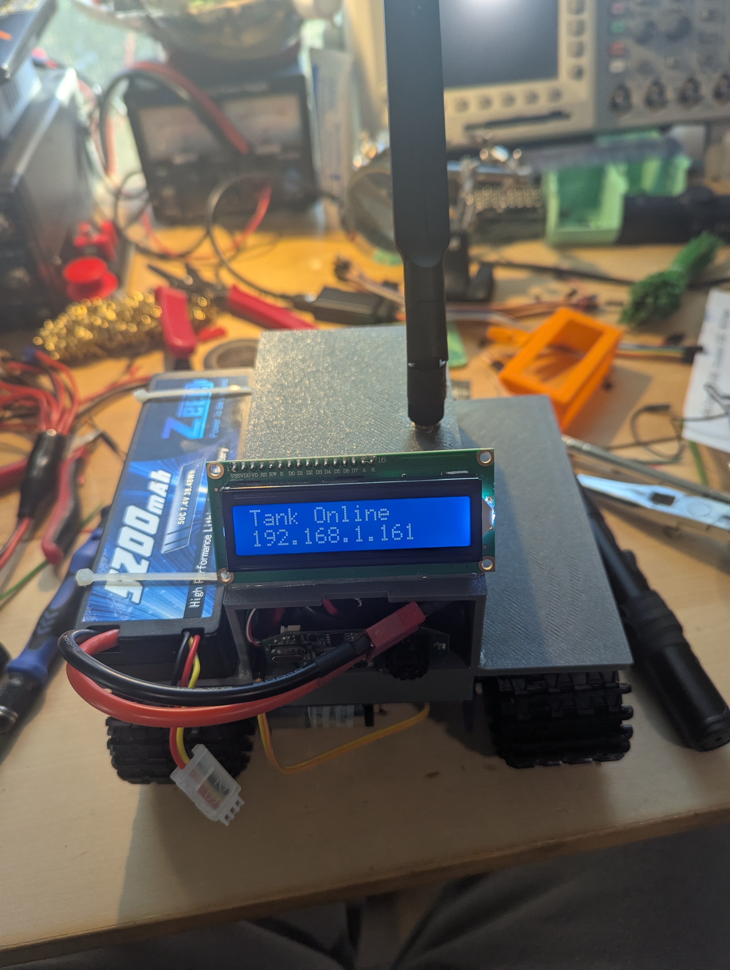
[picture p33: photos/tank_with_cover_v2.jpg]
Cover V2 on tank

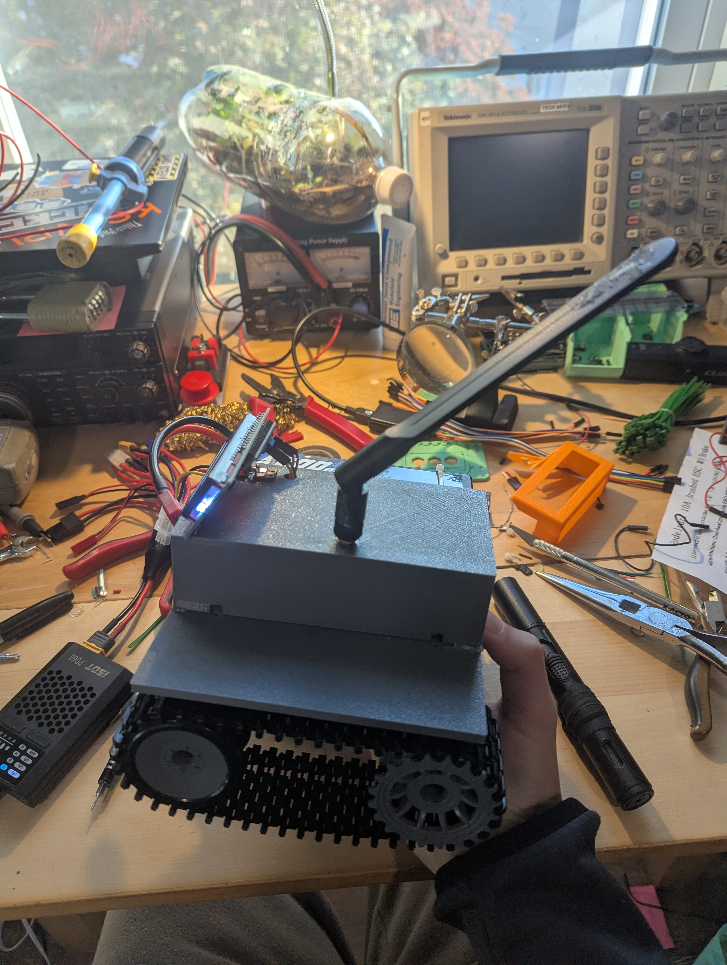
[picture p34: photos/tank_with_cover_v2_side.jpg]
Cover V2 on tank side view


#### 11:00 | 30 minutes

Wrote some quick code that will set the motors to 0 if it has not gotten a cmd in the last 1000ms. To be tested.

#### 20:30 | 30 minutes

Used `sudo nmtui` to set up multiple wifi networks. Then used `nmcli c mod "mypreferred" conn.autoconnect-priority 10` to set priority; higher number is higher priority. The modem has not been set up yet but thats the idea. I'll set up the modem once I have the tank working better on wifi.
| Network Name | Priority |
| --- | --- |
| home1 | 10 |
| home2 | 10 |
| phone | 20 |
| cell modem | 30 |

#### 21:00 | 30 minutes

Spend a bit trying to debug why it is sending tiny bit of power to the motors whenever we read from camera. Seems to be either power related or USB interferince. Tmrw I'll look at the pwm signals to check how they look, as well as calculate the total power everything is drawing and the total the motor contolers can supply from the 5v rail. I think I'm pulling too much so might need a seprate buck converter.

### Monday, October 20th | 30 minutes

#### 07:20 | 30 minutes

Did some research on how much power everything draws. (Everything @ 5v). Each BEC provides 1A so 2A total. A lot of the items did not have stright answers so I'll measure myself at some point. The Pi claims it uses 2.5A but thats crazy so I'll say 1A. Next I'm going to look at the pwm signals to see if there is anything weird about them.
| Device | Power |
| --- | ----- |
| RPI | 1A |
| Modem | 2A |
| Camera | 200mA?|
| LCD | 22mA? |
| Total | 3.2A |

I think all the weird issues are becasue we are drawing too much power from the ESC BEC's. So I'm going to find a better buck comverter to use. In the mean time I'm going to work on the website or something that is not broken.

### Tuesday, October 21st | 1 hour

#### 20:00 | 1 hour

Worked on the website.
Changes:

- Add background
- Fix setting div's
- Add switch for cam on / off (Still working on looks)

### Wendesday, October 22nd | 1 hour

#### 20:00 | 1 hour

Found a buck converter and did some testing to get it ready to be used in the tank. Also started thinking and calculating the correct size fuse to add to the battery.

### Friday, October 24th | 2 hours

#### 17:40 | 30 minutes

Designed V4 of riser. Made the whole thing widers and added holes for the cover to screw into.
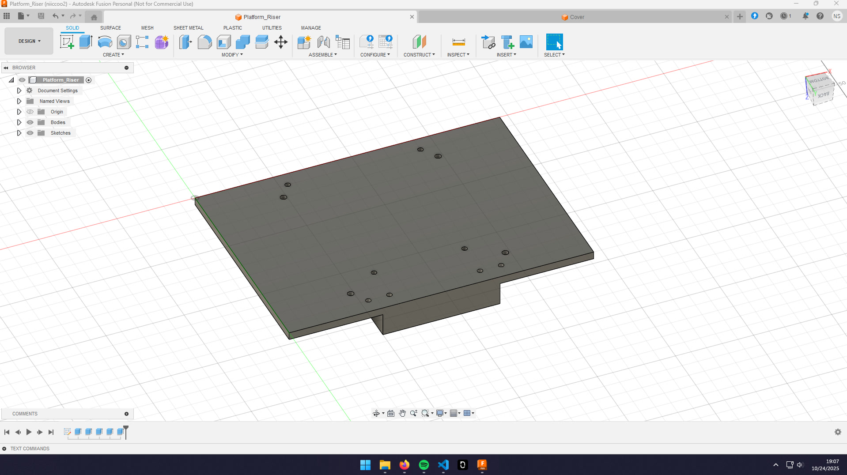
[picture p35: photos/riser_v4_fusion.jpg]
Riser V4 in fusion


### 20:00 | 1.5 hours

Designed V3 of the cover. Main change were the screw holes so I don't need to use hot glue each time I want to mount it. Tmrw morning I'm going to finish some tests on the new buck converter and mount it, along with a fuse and main power switch into the tank. Then mount new cover and see if it fixed anything.
Changes:

- Add hole for GPS SMA connector.
- Add new walls
- Add hole for batt cord
- New hole for new power switch
- GPS and CELL labels
- Screw mounts

### Saturday, October 25th | 1.5 hours

#### 10:00 | 1 hour

Assembled and attached the new riser. I made the holes for the M3 screws a bit too big (3.4mm from 3mm), so that was a mess. Right now you have to take the whole tank apart to replace the riser, not the best, so I might fix that in a new version.

#### 12:00 | 30 minutes

Kept testing the buck converter (forshadowing, it was broken), it was not making sense why the voltage would colapse as soon as a load was added (24 Ohm power resistors).

### Sunday, October 26th | 2 hours

#### 10:00 | 1 hour

Found out that the buck converter I was trying to use was damaged. After I found that out and got some new ones, everything was making much more sense. The converter was able to buck a 6v input to 5v out. That is better than the specs but thats good. It was also able to power some 24 Ohm power resistors. I=V/R 5/24=0.204 ish Amps.

#### 22:00 | 1 hour

Soldered the new buck converter, fuse, and power switch into the tank. Now I need to fit this mess into the new cover I printed... After being powered on for a few secs, something starts making a weird noise, I'll look into it in the morning.

### Wendsday, October 29th | 1.30 hours

#### 20:00 | 1.30 hours

Finished making the main page look nice. Also made the IP picker screen, so when you open the site, you can just type the current ip instead of editing code. Now have to figure out why the camera is not streaming.

### Thursday, October 30th | 2.5 hours

#### 06:40 | 1 hour

Finaly put the cover on the tank, it involved a lot of pushing hard, so I'll make the next version of the cover much taller. I also need to make all the m3 screw holes smaller. And need to space the cell and GPS connectors apart more. It looks likes it's powering on but never connects to tailscale so I'll fix all of this after school.
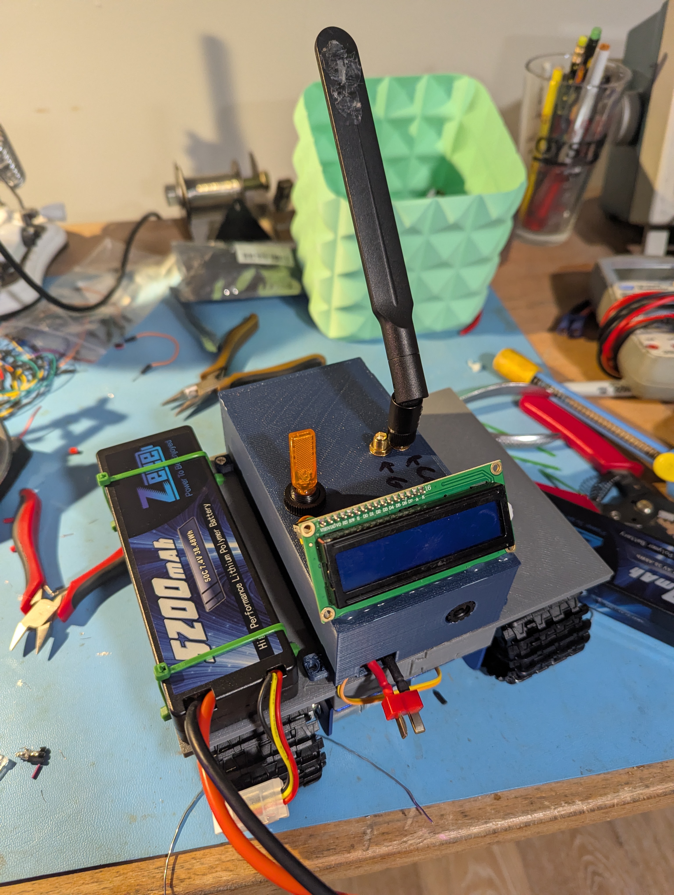
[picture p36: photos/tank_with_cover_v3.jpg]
Tank with cover V3


#### 21:00 | 0.3 hours

Figured out why the tank is not working... I may have snaped the SD card. Just reflashed a card an now am going to set everything up again.
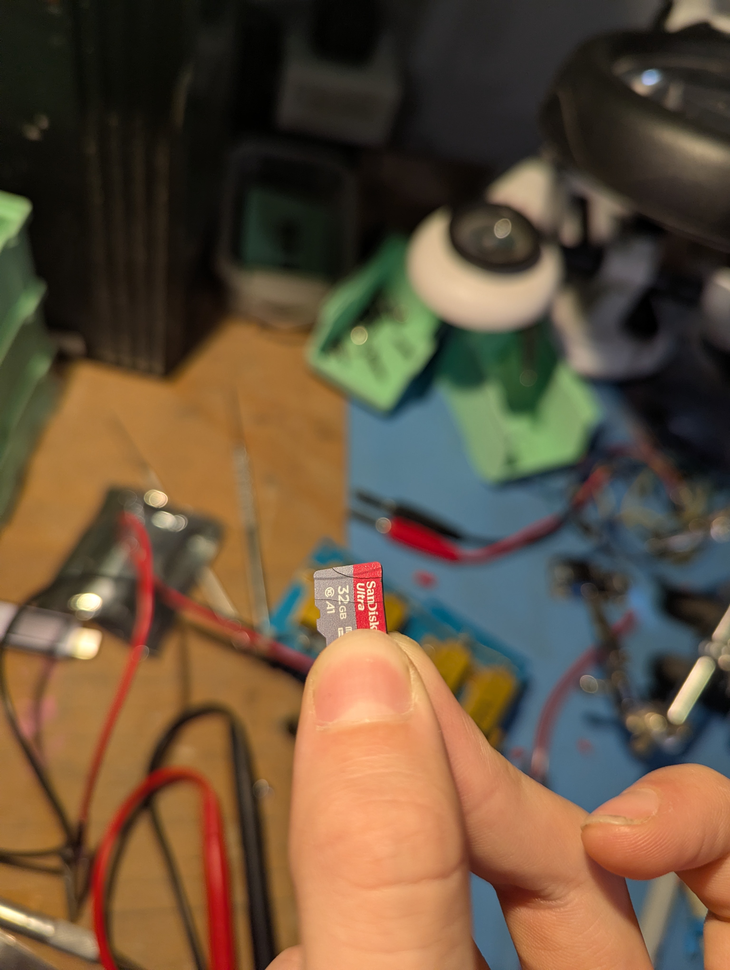
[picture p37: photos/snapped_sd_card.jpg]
Snapped SD card


#### 21:30 | 1 hour

Set everything up on the pi. Also wrote some instructions for setup to help me and or others next time. Debugged some issues with the website, need to make it only try to run any of the functions that use ip once the ip is set. It's also really laggy, but I'll fix that in the morning.

#### 22:30 | 0.2 hours

~~Site seems to not work when hosted on vercel, only works on localhost. This is probably due to the fact that its trying to call the API requests from the backend, not the client.~~ I think that was just becasue the site was not working in general... Anyways, fixed the site, so now you can enter the IP and it actually tries to connect.

### Saturday, November 1st | 3.5 Hours

#### 12:00 | 1.5 hours

Did some debugging. Got the timeout feature working. Also changed the amount the website sends motor cmds from every 10ms to every 100ms. That helped with the lag a lot. Added a thing on website to change that value.

#### 15:00 | 2 hours

Wrote code to let you control the tank like a car, also added switch to turn that on and off. Refactored the whole python file to use classes. Got a bit of help from AI to reduce video bandwidth. It now looks rlly bad, and feels the same on latency, but the bandwidth is down by A LOT.

### Sunday, November 2nd | 3 hours

#### 10:00 | 2 hours

Spent forever trying to get ppp (network over serial) working on the modem. The modem itself will get an IP from the cell towers, but once I start asking for a ppp address, I get ghosted. I had the same issue with this modem on my last project, and I was naive to think it would work better this time. The solution is to use usb, but I'm already using the one usb port for the camera, so I'll have to wire up a hub.

#### 15:00 | 1 hour

Tested the car on it's first long range test. It uhh worked. But the latency was annoying, a lot of the time it was usable, but with color off I coulden't tell the difference between the road and dirt, so I turned on color, that broke everything. I hope it works better once I'm back in Boston, but I don't want to get my hopes up too much. Another issue is not a bug, but once your on the road, it feels SUPER slow. It's fine in a house but once you are on the street its wayyy too slow. So I'm going to start designing a new chassis made out of aluminum extrutions, with a higher speed and more room for goodies.

New things for v2:

- Bigger chassis
- Switch to electon so we can use the hosts serial ports for radios and such
- Faster top speed

### Monday, November 3rd | .5 hours

#### 17:30 | 0.5 hours

Tested the tank in Boston (hopefully has faster cell). It worked, but has a lot to be wanted... It was night so I could bearly see what I was doing. [filz.cc/f/UVyD.mp4](https://filz.cc/f/UVyD.mp4) [filz.cc/f/diph.mp4](https://filz.cc/f/diph.mp4)
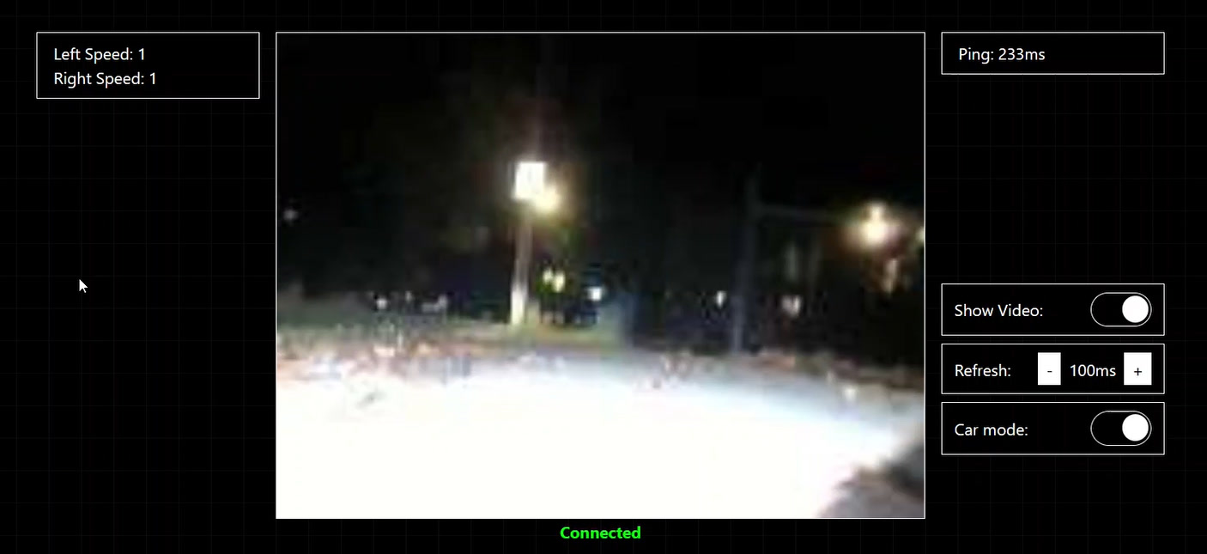
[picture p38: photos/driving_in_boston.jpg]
Driving in Boston


## **VERSION 2**

### Tuesday, November 4th | 1.5 hours

#### 17:00 | 1 hour

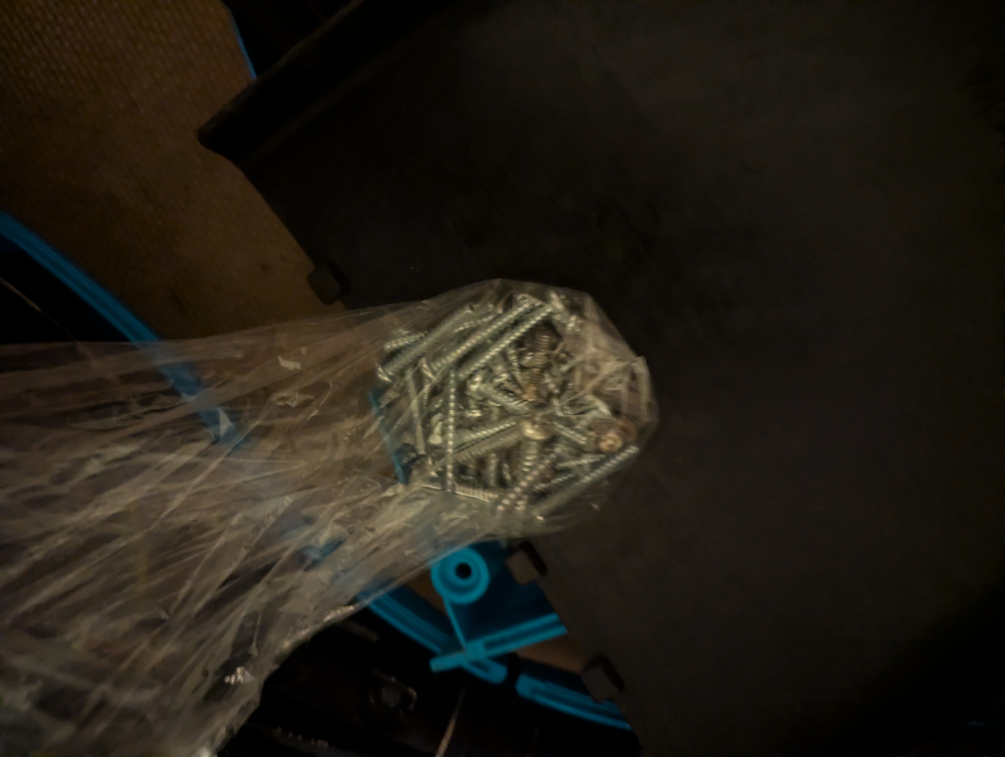
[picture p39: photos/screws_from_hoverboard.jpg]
Wayyyy too many screws
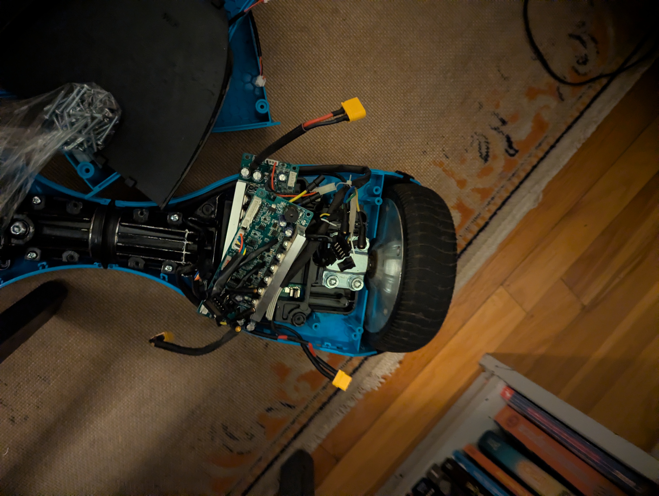
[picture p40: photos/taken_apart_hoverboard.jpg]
Taken apart hoverboard
Started by checking btop (better htop) to see cpu usage while running the script. THe cpu is around 10% when running, so we don't need a faster pi. Then I took apart a hover board to get to the brushless motors, this is going to be the main motors for V2 until I feel I need better ones.  

#### 20:00 | 0.5 hours

Started thinking about how to design the robot and doing the cad. Right now I'm stuck on the suspension because I rally have to build around it. CAD is hard :/

### Wednesday, November 5th | 1.5 hours

#### 07:30 | 0.5 hours

Started reading about WebRTC and how to use it, seems helpful due too variable bitrate among other features. Just built out more in general. To use this libary I found, it looks like I need to switch to FastAPI so I started doing that. Later today I'm going to build the frame for the bigger chassis. It's going to be really simple to start, just a rectangle, but it will be much bigger and allow me to start getting the motors working.

#### 21:00 | 1 hour

Found this repo that looks good, it will let me use the motor contolers already in the hoverboard mobo. I might make the robot in to a hoverboard for now so I don't need to get more parts, depends on if the repo will do the balance, if not, I'll jsut use the motors and mobo. I'll look into a bit more in the morning and figure out my next steps for hardware. [Repo Link](https://github.com/RoboDurden/Hoverboard-Firmware-Hack-Gen2.x-GD32)

### Thursday, November 6th | 2.5 hours

#### 07:00 | 0.5 hours

Wired up this ESP8266 to flash the new firmware to the hoverboard boards. Also got headers ready for the boards. Now i just need to solder the headers and flash it, but the pins for flashing are a weird size so the headers don't want to solder.

#### 17:00 | 1 hour

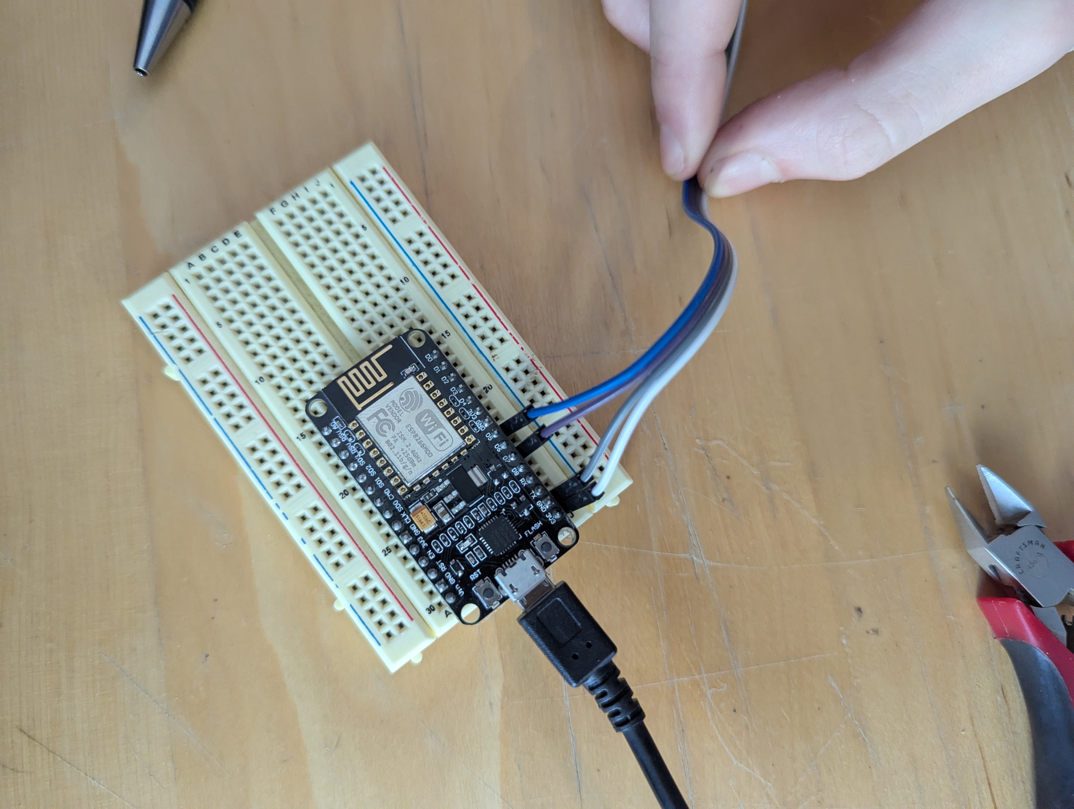
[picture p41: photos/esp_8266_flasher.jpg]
ESP8266 I'm using to flash the hoverboard
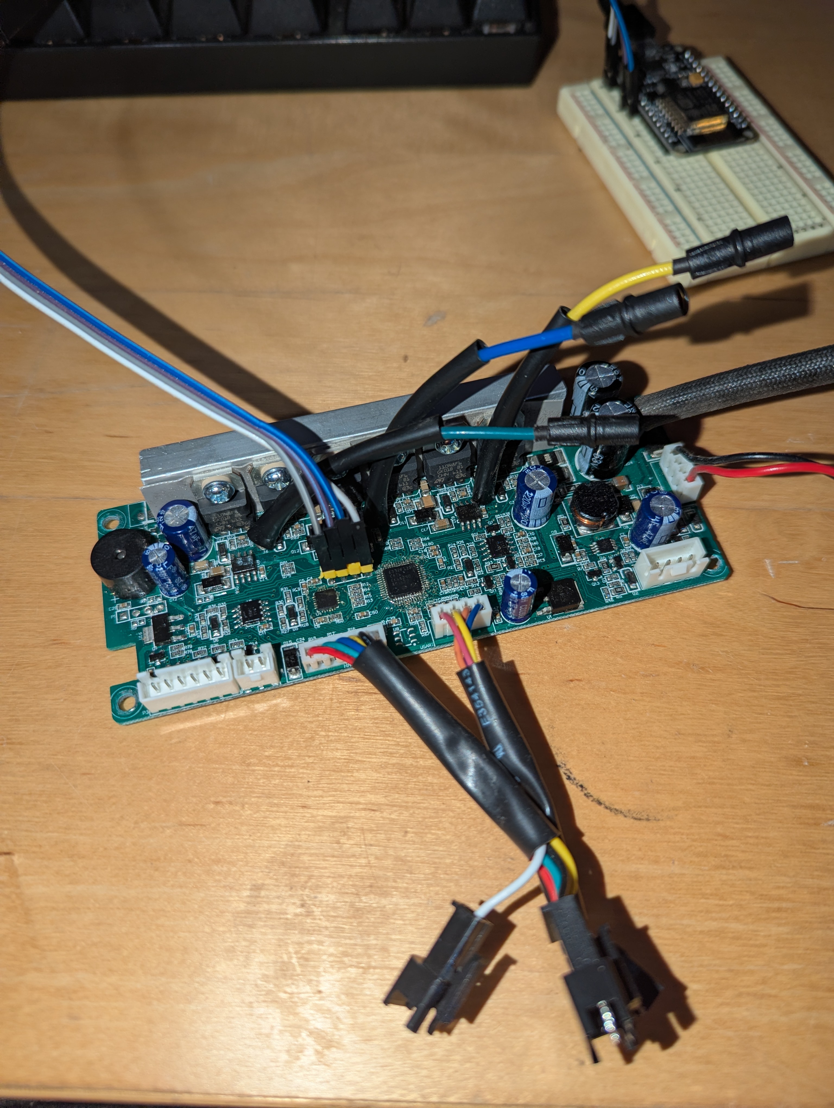
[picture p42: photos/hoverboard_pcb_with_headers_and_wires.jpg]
Hoverboard PCB with nice headers I added
Soldered headers to the hoverboard PCB's to flash. Now I'm trying to follow the **not very helpful** guide in the repo on how to set up the flasher and all that. I have about 20 programs open rn and bearly know what half of them do...  

#### 21:30 | 1 hour

Set up Keil and some other apps to try and program it. I'm making no progress though. I think I'm going to try and use a rpi pico instead of ESP8266 and start over tmrw.

### Friday, November 7th | 2 hours

#### 20:30 | 1 hour

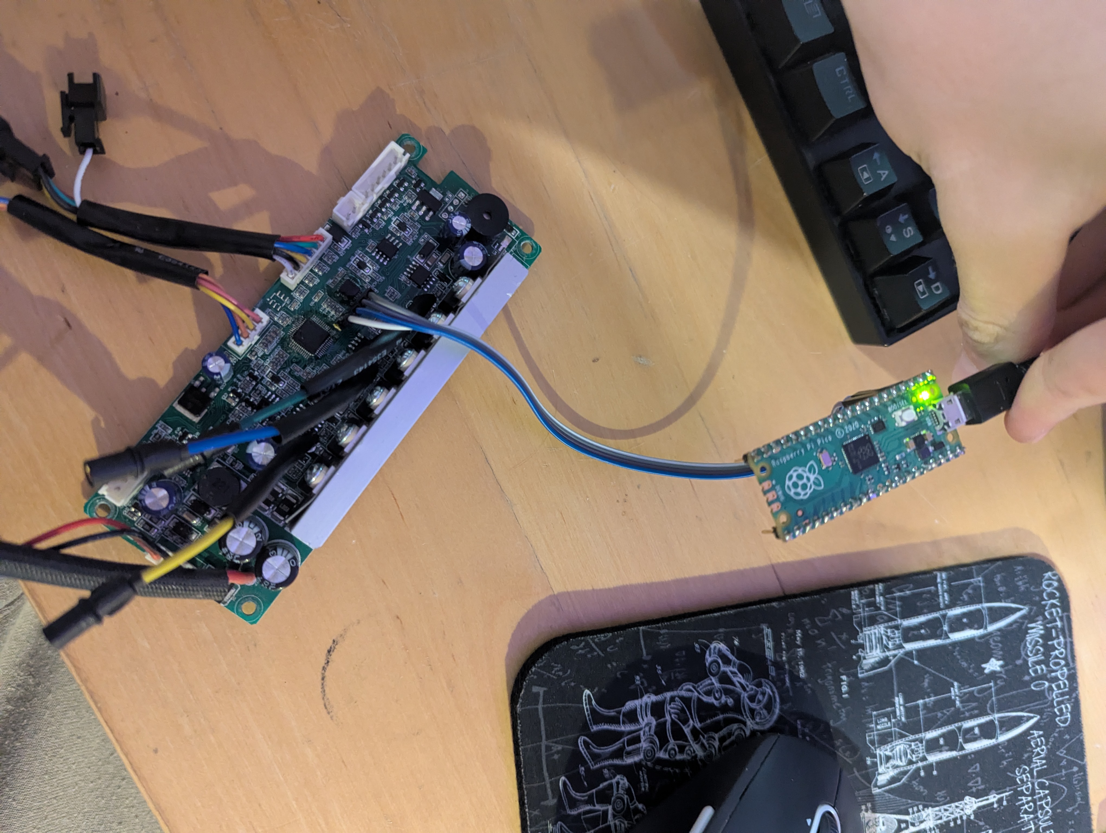
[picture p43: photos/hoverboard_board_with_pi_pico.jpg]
Hoverboard connected to picoprobe
Started by flashing (WHY FLASH SOO MANY THINGS TODAY :/ ) a rpi pico with picoprobe, a SWD flasher that runs on a pi pico. Then I spent a while figuring out what program I use to flash the new firmware to the hoverboard. After a while of it not working, I found out that I was trying to wipe the wrong type of chip. Once I started using the correct chip, I just had to use shorter wires and IT WIPED THE CHIP. :yayayayay: Now I'm going to try to flash the new firmware and see if it does anything... 

#### 22:00 | 1 hour

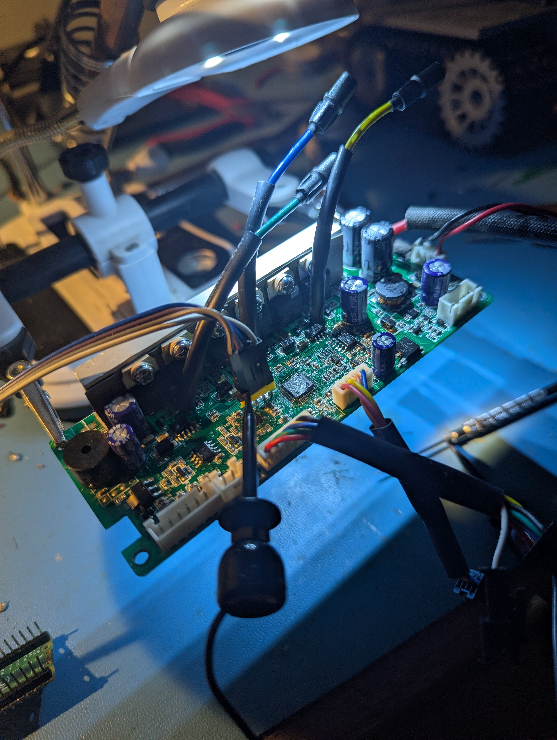
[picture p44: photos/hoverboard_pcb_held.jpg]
Pcb in question
Got stuck with [this](https://github.com/pyocd/pyOCD/issues/1396) error, will try again in morning. I tried grounding the reset pin as it says to, but that doesn't do anythign about the error, it just pops up as soon as I let go (therefore starting the mcu). 

### Sunday, November 9th | 2 hours

#### 16:30 | 2 hours

Susfually compiled firmware from scratch, and tried to flash, no diffrence. Tried pulling boot0 high and low on boot. Tried external 36v power. Tried on other PCB that has not been messed with. Went back to ESP8266 with Keil and flashed with same error. STLink app does not work with ESP8266 or rpi pico.

Fet is `110n8f6` according to google is 80v 80a?

Next steps:

- Try STLink programmer
- Find other repos doing same thing
- Look into price of other motor contollers and or motors

### Thursday, November 13th | 1 hour

#### 20:45 | 1 hour

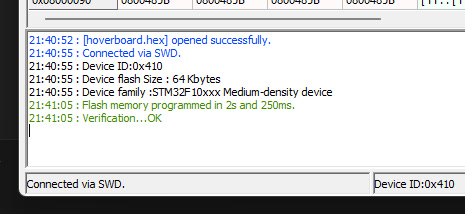
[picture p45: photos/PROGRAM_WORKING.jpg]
Programing working
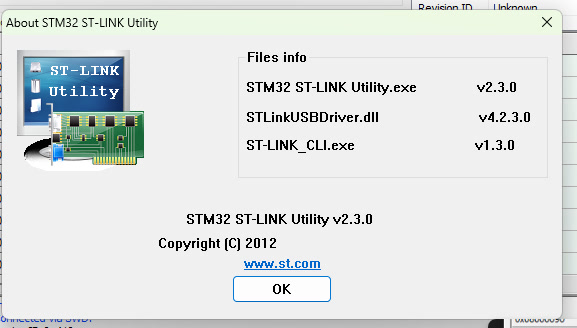
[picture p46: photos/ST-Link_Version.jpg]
ST-Link Versions
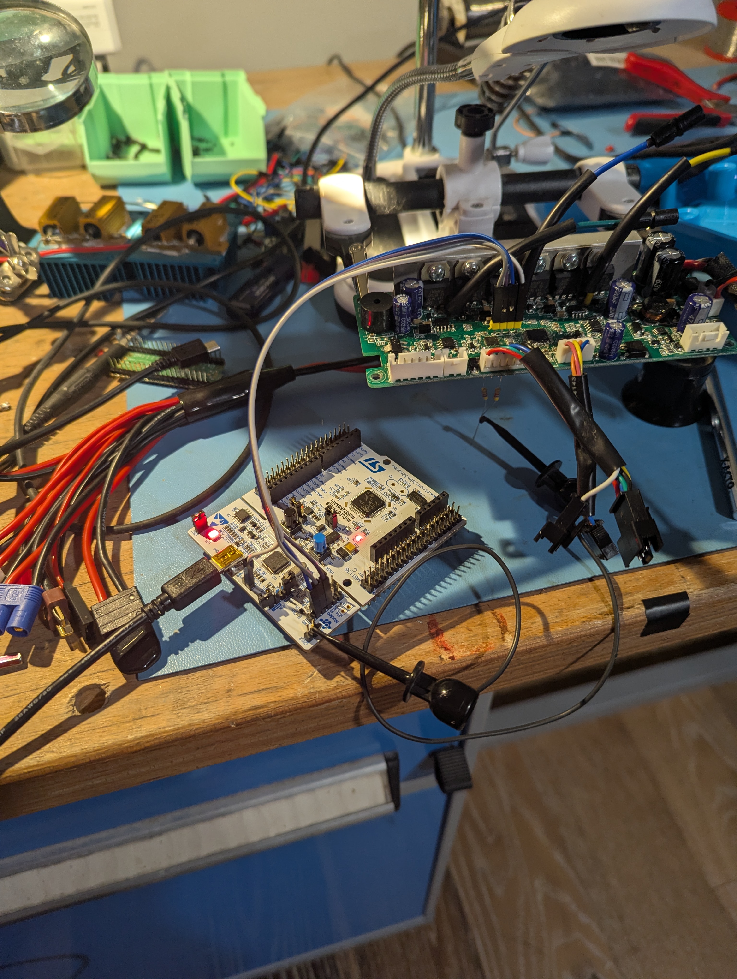
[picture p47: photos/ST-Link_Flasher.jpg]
Flasher
I GOT IT TO PROGRAM!!! Using the ST-Link flasher was the fix!! I have been stuck on this part for almost 2 weeks (of not everyday work) so this is good. To tired rn, but next time I'm home I'm going to test the motors with the boards.   

### Wendsday, November 19th | 1.5 hours

#### 20:00 | 1 hour

GOT THE THING FLASHING LIGHTS WHEN I SPIN MOTOR!!! This is mainly so I don't forget, but when programing, start with only 3v3 from programer, then after the programing disconnect 3v3 and use 36v mains (12v seems to work fine). Now I'm going to see if I can get it to spin the motor!

#### 21:00 | .5 hours

Can't get it to spin motors, when I give it power, the motors seems to stiffen though, so somethings happening. Next steps are to flash the pit detection firmware so I can make sure I'm using the right pins for the hall sensors or smt. I think thare should be 3 lights switching when I spin the wheel, not two. So tmrw I will wire an esp32 to see the output of the autodetect firmware! [Video!](https://filz.cc/f/YVN7.mp4)

### Thursday, November 20th | 3.25 hours

#### 07:30 | .5 hours

Made a cable to connect the ESP8266 for commands and debug info, but now when programing, I get this error: `STLink USB communication error`. No idea why because I have not changed anything. Tried diffrent cables with no sucess.

#### 16:45 | .25 hours

Got it programing again, here is the full process you have to do: first, connect all pins but make sure the 36v power is OFF. Power via programmer 3v3. Then in ST-Link, click connect, it should load some data. Then load your file and click download when it asks you to. Then disconnect the 3v3 from programmer, and turn on 36v power to test.

#### 17:00 | 1 hour

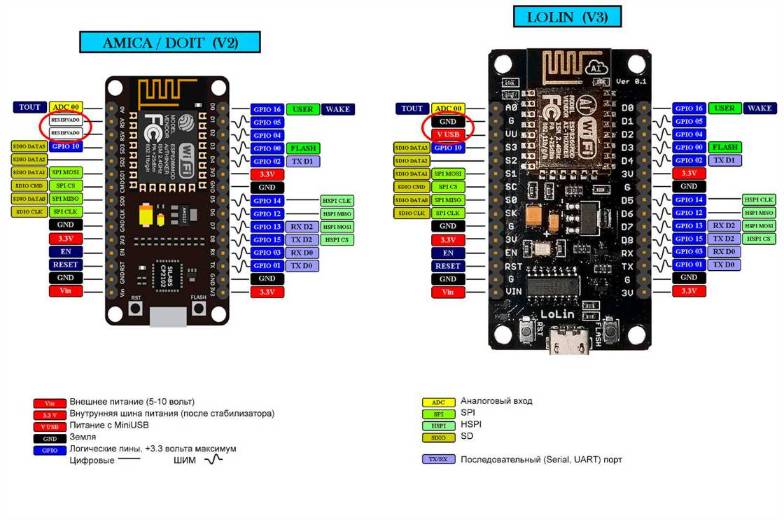
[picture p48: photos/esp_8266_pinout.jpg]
ESP8266 Pinout


| SWD | Pico  | Pico Board | ESP | ESP Board | Color  |
| ----- | ----- | --- | --- | --- | --- |
| SWCLK | GPIO2 | 4 | GPIO14 | D5 | Blue |
| SWDIO | GPIO3 | 5 | GPIO13 | D7 | Purple |
| VCC | 3V3 | 3V3 | 3v3 | 3v3 | White  |
| GND | GND | GND | GND | GND | Gray |

**Keil installation folder:** `C:\Users\wev\AppData\Local\Keil_v5`

We have the `gd32f130c8`

Packs go here: `C:\Users\web\AppData\Local\cmsis-pack-manager\cmsis-pack-manager`

**Green = pink on original cable**

| Color  | Meaning | GPIO | Pin# |
| --- | --- | ---- | ---- |
| Green  | Ground  | GND  | GND  |
| Blue | 5v | 5v?  | 5v |
| Orange | PA2? | 14 | D5 |
| Yellow | PA3? | 12 | D6 |

[This](http://www.hiletgo.com/ProductDetail/1906570.html) has some good info about how to set up the board.

So I got the firmware on the ESP32 so we can see the output from the pin autodetect firmware. I am seeing nothing but there are a lot of things to check. Rn it looks like it only draws current when holding the on button...

#### 18:00 | .5 hours

Compiled the firmware myself and in config selected the pins I'm using for output, now I get messages in the serial console. Still have to hold the button but tis not that bad.
Figured out that `#define LAYOUT_SUB 19	// Layout 19 means x.1.9`.
Anyways rn its still not spinning but I figured out how to get the autodetect firmware running and how to edit all the code. So hopefully it works tonight!

#### 21:00 | 1 hour

Can't tell if the dummy mode is actualy trying to spin the motor. Rn only 2/3 leds light up for the phases... Ideas for tmrw:

- Test with python UART
- Use STM Var viewer thing

### Sunday, November 23rd | 2.5 hours

#### 20:00 | 1.5 hours

Decided to try and use STM Studio to watch the vars like in the guide. After I got it installed, and then added some stuff to PATH, I got this error. I got it watching the vars, but nothing was happening. My next idea was try changing the hall sensor pins to ones I knew was wrong, this made no change, giving me the idea that its not compiling for the right board. I added a debug message to 2-1-9 and it never ran so I messed with the options a figured out how to select the correct one: `#define LAYOUT 9 // means 2.1.9`

#### 22:00 | 1 hour

When it uses the correct files with what I thought was correct hall pins, the leds dont light up at all, and I feel no resistance on the motor. I should see what the pins are on the file I was doing by mistake and use those.

Just tried the halls from the file I was wrongly using (2-1-2) and it did not work. This is good though, so it has to be something else in 2-1-2 but not halls so we can use new halls. Now I am using all settings from 2-1-2 BUT used proper led mappings are we can see all the halls. [Video](https://github.com/niiccoo2/RC-Tank/raw/refs/heads/main/photos/working_hall_with_led.mp4) Still don't know why its not trying to spin...

Switched the `Brushless Control DC (BLDC) defines` and it did nothing, so I think its just not trying to spin at all.

IT SPINSSSSS!!!!! All I did was switch out this bit from 2-1-9 and it started working!!!!!! [Video](https://github.com/niiccoo2/RC-Tank/raw/refs/heads/main/photos/IT_SPINS.mp4)

```
// GD32F130 USART0 TX/RX:	(PA9/PA10)AF1	, (PB6/PB7)AF0 , 	(PA2/PA3)AF1 , (PA14/PA15)AF1 GD32F130x4 only!
// GD32F130 USART1 GD32F130 TX/RX: (PA14/PA15)AF1 , (PA2,PA3)AF1	, (PA8/PB0)AlternateFunction4
#define USART1_TX		PA2
#define USART1_RX		PA3

#define VBATT	PA4		//maybe
#define CURRENT_DC	PA5		//maybe

#define SELF_HOLD	PB2		// rhody tested
#define BUTTON		PC14 	// rhody tested

#ifdef HAS_BUZZER
  // Buzzer defines
  #define BUZZER	PB9 // rhody tested
#endif
```

### Monday, November 24th | .33 hours

#### 07:40 | .33 hours

Figured out how to turn off the buzzer. It's really annoying. Next steps:

- Get UART control working
- Set up on other board
- Get UART bus working to control both boards with one ESP8266

### Wendsday, November 26th | 3 hours

#### 16:00 | 1.5 hours

Made some code to send the uart stuff from pi, still not working. Next steps:

- Flash and get known good code working on esp8266

#### 20:00 | 1.5 hours

Got it to kinda spin via uart. Rn it spins but at a really weird interval. Next steps are to go back to the rpi and see if I can get it to spin, then tune the code more. Then get it working via uart bus. Then start working on the frame (wood or metal) and figure out hte battery and steering I will use for the first test in NH this weekend.

### Thursday, November 27th | 4.5 hours

#### 11:40 | 1 hour

Did a good bit of debugging, so from the var viewer, it looks like every time it starts spinning it gets a speed set, then it times out so therefore the slow down. Now need to figure out why its timing out.

#### 14:00 | .5 hours

Still cant get python to work... This is the data of the semi working code... Also don't know why its timing out...
Semi working data

#### 18:00 | 3 hours

Got it to follow cmds! I had to switch from 19200 to 4800 buad. Now for the time explanation: First spend a while understanding how the code worked. Code in question:

Old code:

```cpp
void RemoteCallback(void)
{
  uint8_t cRead = USART_REMOTE_BUFFER[0];
  //DEBUG_LedSet(SET,0)
  //DEBUG_LedSet((steerCounter%20) < 10,0)	//
  if (	(iReceivePos<0) && (cRead == '/'))	// Start character is captured, start record
  {
    iReceivePos++;
  }

  if (iReceivePos >= 0)		// data reading has begun
  {
    aReceiveBuffer[iReceivePos++] = cRead;
    if (iReceivePos == sizeof(SerialServer2Hover))
    {
      SerialServer2Hover* pData = (SerialServer2Hover*) aReceiveBuffer;
      //memcpy(aDebug,aReceiveBuffer,sizeof(SerialServer2Hover));
      //if (1)

      nicoRxCRC = pData->checksum;
      nicoCalcCRC = CalcCRC(aReceiveBuffer, sizeof(SerialServer2Hover) - 2);

      if (pData->checksum == CalcCRC(aReceiveBuffer, sizeof(SerialServer2Hover) - 2))	//  first bytes except crc
      {
        iTimeLastRx = millis();
        bRemoteTimeout = 0;
        speed = pData->iSpeed;
        steer = pData->iSteer;
        wState = pData->wStateMaster;
        wStateSlave = pData->wStateSlave;
        //if (speed > 300) speed = 300;	else if (speed < -300) speed = -300;		// for testing this function

        ResetTimeout();	// Reset the pwm timout to avoid stopping motors
        iReceivePos = -1;
      }
      else
        iReceivePos = -2;	// skip next start character in case there was another such char in message
    }
  }
}
```

New code:

```cpp
void RemoteCallback(void) {
    uint8_t cRead = USART_REMOTE_BUFFER[0]; // Read the incoming byte

    // Log raw data into nicoRawData for debugging purposes
    nicoRawData[nicoRawIndex] = cRead; // Save the raw byte
    nicoRawIndex = (nicoRawIndex + 1) % 128; // Move to the next index, wrap around if the buffer is full

    // If we are in idle state (waiting for start character) and receive the start character
    if ((iReceivePos < 0) && (cRead == '/')) {
        iReceivePos = 0; // Start recording data
        aReceiveBuffer[iReceivePos++] = cRead; // Save the start character
        return; // Wait for further data
    }

    // If data reading has begun
    if (iReceivePos >= 0) {
        aReceiveBuffer[iReceivePos++] = cRead; // Record the incoming byte to the buffer

        // If buffer is full, process the message
        if (iReceivePos == sizeof(SerialServer2Hover)) {
            SerialServer2Hover* pData = (SerialServer2Hover*)aReceiveBuffer;

            // Assign debug values for CRC
            nicoRxCRC = pData->checksum; // Store received CRC for debugging
            nicoCalcCRC = CalcCRC(aReceiveBuffer, sizeof(SerialServer2Hover) - 2); // Calculate local CRC for debugging

            // Check if CRC matches
            if (nicoRxCRC == nicoCalcCRC) {
                // Valid message
                iTimeLastRx = millis(); // Update timestamp of last valid message
                bRemoteTimeout = 0; // Clear timeout flag
                speed = pData->iSpeed; // Extract speed
                steer = pData->iSteer; // Extract steering
                wState = pData->wStateMaster; // Extract master state
                wStateSlave = pData->wStateSlave; // Extract slave state

                ResetTimeout(); // Reset PWM timeout to avoid stopping motors
                iReceivePos = -1; // Reset position to idle (ready for next message)
            } else {
                // CRC mismatch, invalid message
                // Set position to -2 (error state) and wait for the next valid start character
                iReceivePos = -2;
            }
        }
    }

    // Handle failed state (-2): Skip until the next start character
    if (iReceivePos == -2) {
        if (cRead == '/') {
            // Valid start character detected, reset and start recording new message
            iReceivePos = 0;
            aReceiveBuffer[iReceivePos++] = cRead;
        }
    }

    // Handle buffer overflow (unexpected condition)
    if (iReceivePos >= sizeof(aReceiveBuffer)) {
        iReceivePos = -1; // Reset to idle state to avoid overriding memory
    }
}
```

Make sure that both sides were calculating CRC (checksums) the same way, they were. Then added some global vars so I could see the values of CRCrx and CRCcalc. For some reason they are diffrent most of the time. Then spent a while looking at code to understand why they were not calculating the same.

Then hooked up my logic analyzer to look at the raw data. It was the same each time... (Thats good) Picture of data (This is not the final, or correct data). Also hooked up normal scope to make sure it looked clean and not noisy. It was fine.

At this point, I was almost about to restart with another set of code for the hoverboard. But then I decided to do one last thing and change the baud rate from 19200 to 4800 and it worked!!

Right now there are still a few issues with the wheel, other than needing to get it working from a pi (not a esp8266) and needing to use UART Bus:

- Seems to have a very conservative breaking / slow down. Like VERY slow, if you stop giving it cmds, it takes almost 10 secs to stop from speed 400.
- Seems to make a loud noise when running at high speeds, idk if this is because it is hitting my power limits (set on PS) or if its because its floating rn, and not on the ground, hopefully this fixes itself.

Things to do tmrw:

- Fix conservative breaking
- Make sure second wheel and contoller work alone
- UART Bus
- Frame
- Wire the new python code into the old stuff
- Might need to finish getting webRTC working, might just skip that though
- Set up modem with usb ub
- Figure out what >= 14v battery to use for it
- ^ Might need to make harness for two 2s batts

### Friday, November 28th | 6.5 hours

#### 08:00 | 1 hour

Seems to get stuck when going over speed 500... Using BLDC_BC instead of BLDC_SINE fixed it! Now going to test the other motor and contoller alone, then work on uart bus!

Tested the other PCB and motor and they are working the same as first!! Now going to get uart working from the pi.

#### 09:00 | .5 hours

Got UART working from pi, now working on UART bus. Got uart bus working. Now need to test it with two salves and start on the frame. Working UART Bus bytes

#### 10:00 | 2 hours

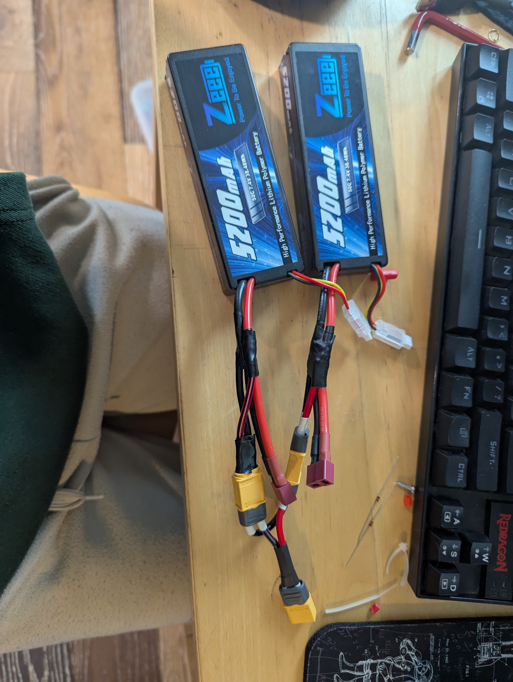
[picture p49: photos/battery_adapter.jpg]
Battery adapter
Did a bunch of wiring. Made a harness to go from 2 2s batts to 1 4s batt. Now working on a 4 way connnector with fuse so we can power everything. Then working on frame. 

#### 12:30 | 1 hour

Took forever but made the wiring harness for the data stuff. Now testing both motors at once. Need to find out how to bypass on button... Just crashed my laptop bc I hooked up power wrone :/ Found pins to bridge so it turns on on power. Got both motors working at once.

#### 15:00 | 2 hours

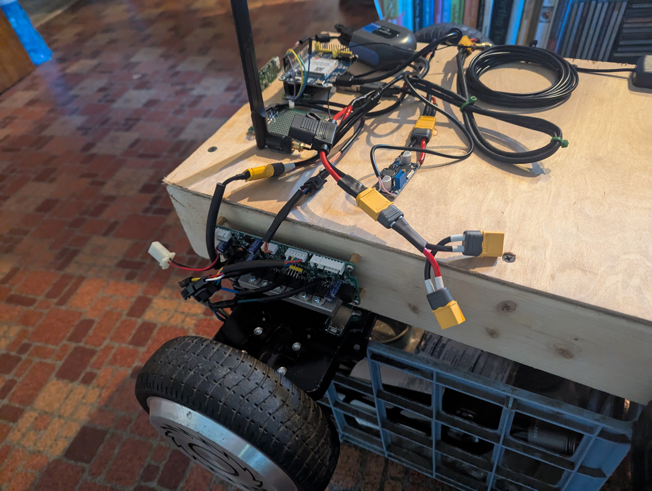
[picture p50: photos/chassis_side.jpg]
Side view of new frame
Made this really nice frame. It looks a bit weird but it works. Then put everything onto the tank and tested that the motors still spin, they do! Tmrw morning I will turn the motor code into a class then integrate. Top view of new frame 

### Satuday, November 29th | 2.5 hours

#### 09:00 | 1 hour

Now working on rewriting the motor control into a class that I can then use in the api thing. Was not too hard, just copied a bunch of code from the test file into the old class. One thing you have to remember is that slave 1 is left and slave 0 is right.

#### 11:00 | 1 hour

When I made the wiring harness for the esc data comms, I made it on perf board, but it was really bad. Thats why sometimes it woul just not listen to the cmds I was sending. So I decided to just solder the wires directly because perf board was a bit too much for the task. After I soldered the wires directly I realized that I still messed up the wiring. This is because from the factory, they switch the data tx and rx in the cable so that the two boards can talk to each other, so I took apart hte connector so I could switch them back. Now the esc wiring should be better.

#### 12:00 | .5 hours

Finally I got to test it, this test was a bit flawed though, because I found out that the usb hub I was using was really old, so it was unable to stream camera data over it. For camera I had someone follow on google meet so I could see what I was doing. Other than me getting car sick from the shaky camera, the test was pretty good, the latency was not amazing, but it was semi drivable. So hopefully once I get a new usb hub, the built in camera will be better! (Video will be from second test)

### Sunday, November 30th | 2.33 hours

#### 10:00 | 2 hours

Spent a while trying to set up WebRTC. It should have much better latency but I was unable to get it working. I just wanted to drive the car so I reverted to using MJPEG.

#### 14:00 | .33 hours

DROVE THE CAR. There are a lot of things to add BUT ITS USABLE!!! Things that happend (so I remember):

- Latency is not horible, but WebRTC is still a good thing to add
- You tend to sverve a lot because of the (even if small) latency...
- Need to figure out how to read bettery voltage. This could be from ESC's or make my own thing.
- I think I broke the webcam because there are PCB trace looking things in my view. It's still driveable but should fix it.

[Video](https://hc-cdn.hel1.your-objectstorage.com/s/v3/c245bbe98e534a92a19db2d41ba9c841da88784e_2025-11-30_13-42-12.mp4)

This is the first part of this project that I am submitting to [Moonshot](https://moonshot.hackclub.com). As of here I am at **65.46** hours!

### After NH test

After the test in NH, I created and painted a nicer wooden frame. Also got WebRTC working, WebRTC was the best change so far. Once I had WebRTC working I was able to do a 7 mile test in Boston.

## **VERSION 3**

### Wednesday, Feburary 25th | 0 hours

#### 20:00 | 0 hours

I'm thinking of starting the project again and adding self driving. If I do, here is a list of things I need to do to get it working again:

- New sim card; unlimited
- Need to set up whatever server I needed for video. Might try to do this with port forwarding at home instead of paying for a vps
- Clean up this readme; might reverse the journal so you don't need to scroll as much
- Add a summary of what I added to V3 (Paint, WebRTC, think I hosted the website?)

Then, once it's all working nicely again:

- Get everything working on coral dev board
- Better headlights
- Start on self driving

Then once self driving is working:

- See how it can go faster
- Nicer frame?

### Friday, Feburary 27th | 0 hours

#### 07:00 | 0 hours

Booted up the tank with the pi zero 2w and am seeing what works! Video seems to work but everything else is weird... Going to debug in a few mins. Thought I needed to get a WebRTC TURN, ICE, or STUN server running, but video seems to be working now... Maybe it's because I'm not on cell yet?

Now fixing the controller mappings bc it's wrong. Now everything seems to be working! Batt voltage reading seems to be a bit slow but other than that its good. Now going to try and get this coral dev board online.

Cable meanings:

| Color  | Meaning |
| --- | --- |
| Orange | Light strip data |

#### 17:00 | 0 hours

Got the coral board up and running with ssh. Now going to rewrite the code to use the coral gpio code.

### Saturday, Feburary 28th | 2.5 hours

#### 10:00 | .5 hours

Starting to rewrite code to coral gpio.

Fixing the GPIO was really easy, just had to change some paths. Going to test in a sec. Was fixing ssh on the dev board. This cmd fixed it `sudo tailscale up --reset --netfilter-mode=off --ssh`.

#### 11:00 | 1 hour

Working on getting things installed... We seem to have some memory issues and it wants to kill ssh a lot...

#### 14:00 | 1 hour

Still working on getting things installed. It seems like google is keeping their distro using older packages for compatibility but that makes some things annoying. Think I'm almost done though.

Things in general to add:

- Make website work without tailscale
- E-Stop button on car

Here is the roadmap for self driving right now:

- Simple waypoint following
  - RTK GPS
  - Planned from website
  - Adding full auto route planner is an idea, but won't affect what the car end does
- Add local vision stuff
  - Stay on sidewalk / safe areas
  - Avoid obstacles

Next step is to either work on the GPS route planning on the website, or once I am with the car, test if the coral board works.

### Sunday, March 8th | 0 hours

Have not had time to work on the tank, but fallout hour tracking started, so going to write some stuff down rn. On Hackatime, RC-Tank is at 32 hours 7 minutes.

### Monday, March 9th | .16 hours

#### 20:30 | .16 hours

Started testing with the coral board. Going to see if we can connect over the site rn.

Still having the webcam issue. Did some testing and `/dev/video0` was something built into the coral dev board, not the camera. Plugged the camera directly into the board and now its showing as `/dev/video1`, going to see if more things work now. If they do then I will figure out why the usb hub is not working.

Still geting camera error... FIXED! Seems like the issue was from the old MJPEG streamer that was in the code. Removed all old code so we only have WebRTC now. Now having a gps issue, think ima just comment that out for now. Or get USB hub working.

TODO:

- Get USB hub working with camera
- Wire motors
- Wire lights
- Start on route planing interface (WEBSITE)
- Get a RTK GPS added and tested

### Tuesday, March 10th | .5 hours

#### 07:30 | .5 hours

Camera is now working with the USB hub! Seems like this mendel linux is giving a lot of issues... The kernel doesn't have some things that we need to use to modem. Not sure what I'm going to to next... Might find a new dev board, but this one seems pretty nice.

Going to look into building my own OS / kernel. Need to enable the USB drivers for the modem, also would be nice if we could have everything up to date.

TODO:

- Make new USB-C power cord
- Wire motors
- Wire lights
- Start on route planing interface (WEBSITE)
- Get a RTK GPS added and tested

### Friday, March 13th | .5 hours

#### 21:00 | .5 hours

Decided to get a Jetson Orin Nano. Finally had time to set up today. Tmr is going to be getting the existing system working with the new device. Then going to get RTK gps waypoints working.

### Saturday, March 14th | 5.32 hours

#### 15:20 | 1.16 hours

Finally have time to work on the tank!! Going to start by regluing things to the wood and wiring the jetson power. Ik that glue is not test best bc it comes undone with heat and bumps but its fine for now.

Wired in the Jetson and new RTK GPS module. Also remounted a bunch of other things. Going to get all the basic functions working again now.

#### 16:30 | 1.33 hours

Found how to switch power modes:

```shell
#Check current mode:
sudo nvpmodel -q
#List all available power modes:
sudo nvpmodel -q --verbose
#Switch to 15W mode:
sudo nvpmodel -m 1
#Verify the change:
sudo nvpmodel -q
```

Mode `0` is 15W, `1` is 25W, `2` is MAXN SUPER. Going to leave at 1 for now.

| Color  | Meaning | GPIO |
| --- | --- | ---- |
| Green  | Ground  | GND  |
| Blue | 5v | null |
| Orange | TX? | 10 |
| Yellow | RX? | 8 |

Think UART 1 is `/dev/ttyS1`

Server is down... Local website is also not connecting... Was because I did not accept the self signed cert.

Jetson Pinout

Got video working. Seems laggy though.

TODO:

- Latency
- Lights
- RTK GPS
- Website route planner
  - Make toggle to disconnect video / make sure that toggle we have works

Latency seemed to be because of the data refresh rate. 200ms seems to work better.

#### 20:00 | 1.33 hours

Have been working on RTK GPS, seems a bit complicated to use with python but am making good progress.

Got temp banned from the site for spam (uhhhh) so going to work on this in morning. Going to try an work on the website right now.

#### 22:00 1.5 hours

Worked on website a bunch, now have tabs. Need to work on route planning and gps in morning.

### Sunday, March 15th | 1.66 hours

#### 09:00 | .66 hours

Going to try and get gps working. No AI this time lol.

RTK GPS is being a pain, going to just do some tests with normal GPS for now.

Got normal gps working.

#### 10:30 | 1 hour

Going to work on integrating the new gps into the codebase, then am going to work on route planning in website, then making it follow that route.

TODO:

- Add video toggle to website
- Simple route planner
- Follow route
  - Calc heading
  - Start with simple self driving mode

Added video toggle, now going to work on simple route planner.

Ended up spending most of today messing with the GPS trying to get it to work...

#### 21:00 | 0 hours

Switching the Jetson from a 32GB SD card to a 512 GB NVMe drive.

### Sunday, March 22nd | 2.5 hours

#### 09:00 | .2 hours

Started working on the route planner... Need to make it so you can click locations, it saves them, and draws lines between them.

Once I have a way to plot locations, will wire up the compass and other stuff...

Still have to get jetson working on ssd.

#### 10:30 | 1.33 hours

Increased max zoom (Leaflet.svelte:39)

Made it so when you click it adds a new waypoint. At some point I should switch from all these REST APIs to webhooks...

Got most of the route planning tab done, you can now add new points, remove points, and there is a button to send them to tank. Need to write the code to send them to tank. Then need to work on tank code to follow them and a basic self driving screen with start, stop, and a console.

#### 14:30 | 1 hour

TODO:

[x] Set new default start location
[ ] Get self driving page on site polling gps and compass
[ ] Maybe add map to self driving page?
[ ] Write code to follow gps
[ ] Find better map tiles that allow more zoom
[ ] Get Jetson booting from SSD
[ ] Add compass

### Saturday, March 28th | 1 hour

#### 12:00 | 0 hours

Spent forever getting the Jetson to boot from NVMe. This was the thing that finally made it work: [jetsonhacks/migrate-jetson-to-ssd](https://github.com/jetsonhacks/migrate-jetson-to-ssd).

#### 18:10 | 1 hour

Going to start by installing everything needed to run the program, then making a `requirements.txt` file.

Now going to make sure everything works, then wire the compass module.

Still stuck on something. I'm not getting any errors, but it seems like it is silently crashing on something before the lights... Not sure what though because this didn't happen last week and I haven't changed anything. There also isn't much it even does before lights, iirc lights are the first thing it does on start...

### Sunday, March 29th | 3 hours

#### 14:00 | 1 hour

Going to start by debugging this issue causing it to not run the script.

Found one issue, not sure if this fixes everything, but you need to remember to use the Jetson-IO python script to configure the pins for SPI data for the lights. Might still have to do this for the motors, not sure yet.

Found other issue. You must be going to HTTP**S**. Not plain HTTP. Then you must accept the unsigned cert. Also make sure you use the :5000 port.

Everything on website seems to be working now. Just need to figure out why the driving screen is off center.

MOTORS WORK!! Now going to figure out how to wire this compass and write a test script. Also looking at the GPS data we should try to get RTK gps working again.

#### 16:00 | 1 hour

Wiring chart for compass:

| Color  | Meaning |
| --- | --- |
| Black  | Ground  |
| Red | 5v |
| Brown  | SCL |
| Orange | SDA |

Wired the compass to the car, now working on some test code to read it.

#### 17:00 | 1 hour

Worked on finding drivers for this compass but couldn't find anything... Going to stop for now and try again later...

### Sunday, April 5th | .66 hours

#### 14:00 | .66 hours

Going to try and get the compass working today.
Ended up getting stuck on this command due to the internet here lol. `scp arch/arm64/boot/Image nico@tank:/tmp/` Once back in mass I'll try to work on this some more.

### Monday, April 20th | 0 hours

#### 19:30 | 0 hours

Theoretically I got the kernel fixed? Not sure, I will test more in the morning.

### Tuesday, April 21st | 2.33 hours

#### 08:00 | 0 hours

I think I broke the kernel last night. Have no idea why is is not booting right now. Going to start fresh with a new flash in SD card and try to restart with all this debugging becuase I don't really remember what I was trying to do last time. It was almost a month ago. Not going to count this time hor horizons becuase idk if it even counts and I don't want to track it.

Think I figured out why the compass isn't working!! Need to export a var when running the cmd via sudo. Like this: `sudo JETSON_MODEL_NAME=JETSON_ORIN_NANO python3 ./test_files/ada_compass_test.py`.

#### 13:00 | 1 hour

Am getting numbers from the compass, they seem to be decent! Going to now write a library for the main code and start outlining the main code.

Have been thinking and I am going to get basic waypoint driving working with the REST layout that we have right now, but once that is working I really need to switch to webhooks (I think thats the right name).

Think a good plan for how to do self driving for now is to just have a function that starts when you call an api with a route. Ofc we need to add logging / telemetry and the ability to stop it, but this should be good enough for now.

Should still definitely add websockets later. Need to finish a few things, but once we have the waypoints, we need to figure out how to calc heading using current position and next waypoint, then use current heading and needed heading to go the right direction.

#### 19:30 | 1 hour

Started by adding other WiFi networks (did not track time for this). Then it took a bit moving everything to SSD and labeling all the connections via GPIO so that it isn't hard to know where everything goes.

#### 20:30 | .33 hours

Lights stoppped working again... Going to fix these then start on calculating bearing to next waypoint using current and final position.

Fixed lights, I may have not read my own guide on how to set up a fresh jetson. I may have also made that guide because this exact same scenario has happened...

### Wednesday, April 22nd | 1 hour

#### 17:30 | 1 hour

Going to start by figuring out how to calulate a bearing using two points on a sphere. One issue is that anything involving spheres gets really complicated... I think I am going to pretend that the earth is flat to make the math simpler. It shouldn't matter much becuase the car isn't going far enough to make a difference and even if it was, there would be many waypoints.

This code is getting really messy, tomorrow I am going to try and transition everything to websocket to make this more simple.

Got the code that calculates heading kinda done. As I am writing, I realize that it will only give numbers from -180 to 180, although that might be fine, not sure yet. Also started reorganizing the python code, it will take me a bit more to get it done but I think it is starting to look much better, and be ready for the websocket switch. Goals for next time are finish cleaning code, then either work on waypoints or refactor to use websockets.

### Thursday, April 23rd | 1 hour

#### 17:00 | .75 hours

Getting no errors with the new code, now going to test that everything is working. Everything is working, now going to look into a better way to do everything than REST API.

Now thinking about how I will switch to websockets. I think it makes sense to have one connection for everything and use prefixes to route it to the correct place. Also now that we have a bidiretional communication channel we don't need to request GPS anymore, we can just send it automaticlly.

#### 19:00 | .25 hours

Worked on websockets a bit. Hopefully I can get everything working on websockets tomorrow and then start working on self driving and or learning how to stay on sidewalks. I think the end goal for this basic self driving is to have it try to follow waypoints while staying on sidewalks.

### Friday, April 24th | 4.5 hours

#### 10:00 | 2 hours

Working on moving everything to websockets right now. Here is a list of things to still move on the server (tank) end:

- GPS
- Health check
- WebRTC

The issue is that some of these work better if the tank just auto sends it every x secs so I need to change that...

So far I have gotten motors, lights, and ping working. Ping took a while because it gets messy when using a single tunnel for communication. WebRTC shouldn't be super hard, I just need to find where we use the API for connecting. The only other thing we need to do is have the tank use a background process to send telemetry every second or so. Then in all the functions that do things like read voltage or gps, instead of returning it, we need to update the values in the telemetry process. Also need to figure out how we should report issues with a command that was sent.

#### 15:00 | 1 hour

Going to start geting WebRTC working again. Have just been thinking about how to remove tailscale though, because I want this project to work standalone without external services, but I think tailscale, or at least something similar will be needed. Also not sure how to set up self driving on the UI side... Anyways those can be figured out once its time.

Done with the hour, ended up learning a lot about promises and await. I am working on a function that will let you send a message and it returns the response. This is useful for things like pings or setting up WebRTC. It adds a lot of flexability so now we can have 3 different messages: one way to tank (motor commands, lights), one way to website (telemetry), and two way linked (pings, items that require a response).

#### 16:00 | 1.5 hours

Just writing this down so I don't forget. The type of a two way message isn't needed from the client (website) end, but it is needed on the server (tank) so that it knows how to process the data. I will keep a type in the resopnse just for uniformity.

Going to take a break now. Stuck on the timing for WebRTC handshake.

### Saturday, April 25th | 1 hour

#### 10:00 | 1 hour

Going to see if we can get webrtc working over WebSockets.

Took a while, but I finally got WebRTC video connecting over websockets. Now am going to figure out why the website says a green `error` at the bottom of the page. But first going to see if webrtc will work using my server as a turn server.

Did some stuff. I got a TURN server working and I think I know what I need to do to get the TURN server working on my own hardware. Going to try and get telemetry working tomorrow.

### Sunday, April 26th | 3.5 hours

### 12:00 | 1.5 hours

Going to start by figuring out why there is a green error message when everything is working. Almost done fixing the green error message, I think I know what is causing it: when it sends to first motor cmd of `0, 0` the WebSocket connection isn't open yet, so it returns false, that sets it to error. It will change to connected if you have a controller plugged in. Also finally added some code to remember the last IP through reloads. It was literally 2 lines of code, and super easy.

Going to start working on getting telemetry working now. I think all we need to send is GPS and voltage now.

Got telemetry sending from the tank, now just need to read it on the website.

### 14:30 | 2 hours

Going to start by getting telemetry decoding on the website working. Got telemetry reading working on the website. Working on getting self driving working right now. One issue I hit is not multiple things are trying to read GPS, so I am going to make a thread that just always reads it and updates to states.

### Monday, April 27th | 4 hours

#### 08:30 | 1.5 hours

Going to start by finishing the basic waypoint code, hopefully we can do some field testing in an hour or two.

Almost done with basic waypoint code, just need to figure out some things with the compass...

Compass code seems to not be working again... Going to try and see if this is because of bad wiring or something else.

Compass wasn't working because ground was not connected. Just spent a bit figuring out how to calibrate the compass and doing that. Then added it to the main compass driver.

#### 11:00 | .5 hours

Did some math for the basic self driving code, now just need to do a bit more and then make the website half.

#### 12:00 | 1 hour

Finished the math that calculates how much to turn for each waypoint, I'm sure I will have to change some constants but it should be good enough. Also added self driving as a service, so now all I need to do is create a page on the website to start and stop it. Might add some of the telemetry there as well if I feel like it.

Added the self driving screen to the website. Right now it is just a copy of the normal driving page with the video removed and motor speeds replaced with a start and stop button.

#### 15:00 | 1 hour

There seem to be a few issues regarding who can control the motor. Sometimes it seems like the self driving thread crashes because it tries to control the motors at the same time as a human driving...

Did a bunch of field testing today and here are the main issues:

- Compass still has a lot of issues
- Waypoint following seems to be pretty good, but still need to add the logic to decide when to go to the next waypoint in the list.
- Now that I think about it, the apparent compass issues could also be from the GPS not being accurate

### Saturday, May 2nd | 4.15 hours

#### 09:30 | 2 hours

Not sure exactly what I am going to work on right now... Going to start by adding logic that tells the self driving when to start going to the next waypoint. I guess I am just going to try and make the waypoint logic better in general... Is raining right now, so I can't test too much, but other things I might do today are: add more stats to self driving screen, figure out why motors don't stop all the way when self driving is stopped, add rtk. The only thing I am worried about with adding RTK GPS is that I don't want an over reliance on it... Although once I have more than just GPS for navigation it won't be such an issue.

Things to do:

- [x] Next waypoint logic
- [x] Stop motors after self driving ends
- [ ] Better debug system
- [ ] RTK GPS
- [ ] More self driving screen stats

Going to start by writing a functoin to calculate distance between two sets of coords. Then will say something like if within x distance, go to next waypoint.

Changed the `states.waypoint_locations` (waypoint list) to use the normal `Location` type (formerly `GPSLocation`) instead of the now not used `WaypointLocation` type (formerly `Location`). To do this, the locations are converted from `WaypointLocation` to `Location` when they are received in the websocket handler, before they are added to the `states.waypoint_locations` list. Now that locations are all one type, it will be a lot easier to write the distance calulation function. Going to start with a simple function that finds distance, but the issue is that it will be in whatever unit the coords go in as, so we will need to convert that to meters after, and make sure to define this in the doc string.

Should be done with the logic that lets it switch to a new waypoint. Although I'm sure there will be issues when I test it.

#### 12:00 | .75 hours

Working on debugging the motors not stopping and found another issue. It is of the same nature but not sure if this will fix the same fix as self driving. If you are driving and then switch tabs it doesn't stop, this could be because of the website still sending pings or the timeout isn't working. But now that I say this, I don't think I wrote it to stop here... So it's an issue but I'm not sure if I ever did anything about it. Does a similar but different thing when going to another page on the site. So I think we have 3 issues that seem the same but are for 3 different reasons.

| Steps to cause | Notes | Done? |
| --- | --- | ----- |
| Go to different tab | Looks like the website is still periodically sending motor commands | [x] |
| Go to differnt section | Looks like motors so the slow spin thing | [x] |
| Stop self driving | Motors do a weird fast version of slow spin | [x] |
| Failsafe | Seemed like it should have caught the past issues | [x] |

Going to start by fixing the different section thing. Now that I think about it, when you go to a new section, it stops sending motor commands, but never says zero. But then the failsafe should be starting anyways.

Think I figured out how to stop the motors when switching tabs, but I still want to do some testing on the failsafe to make sure it is working... So adding that to the list.

Fix did not work... But timeout is working now?? Idk, I don't like how weird all this is.

#### 16:00 | 1.5 hours

Just tested and was able to reproduce the failsafe not working.

I'm really slow, first, I wasn't on the local version of the site, and second, there is literaly a function that runs when switching tabs. Now it does the same weird thing that happens when you stop self driving, so I am going to assume the rest is the same issue.

Seems like the ESC's sometimes need more than one instruction to get an idea of what to do. This doesn't really matter if it misses something when driving, but when you send it one command to stop, then it is an issue. Also would be nice if we could get their baudrate turned up so that we can do more messages.

Omg, different section seems to be broken again. Also it really should be failsafing a lot of these times. Weird, after a reboot (for other reasons) the section switching seems to work again... Not sure why so I'm sure it will come up again. Also, the failsafe only seems to be happening when you send a single instance of a 0 and the ESC's don't listen... Then ofc the failsafe works... Now it is time to work on fixing the weird slowing down when it only sees one instance.

The fix for the motors not always stopping when they only get one command isn't a really good fix, but should be good enough. I just changed it to send a special command for stop and if it gets it it sends stop, waits, and sends it again. I think the core issue is more something in the ESC, which I should mess with later this week once I have all my stuff I need because I now have a few things I need to fix on those ESC's.

Fixing the timeout was super easy, and now that I think about it, it also should be a janky fix to the ESC's turning off. I just removed the thing that makes sure it isn't already stopped. I don't even know why I had that, because it doesn't really do anything with how the program is set up right now.

Found a few issues that I caused. I was using a different number than what I thought I set the stop code to. I got self driving stopping before the timeout hit, so I am going to call that good enough for now. Might work on this a bit more later today, but now sure.

### Sunday, May 3rd | 3 hours

- [x] Better debug system
- [ ] RTK GPS
- [ ] More self driving screen stats

#### 07:45 | .5 hours

Going to start by making a better debugging system so that it isn't spamming things that I don't want. I want to make it so if I run it with a flag like -motors-debug, then it will do motor stuff, but nothing else.

Think I got the better debugging working! Going to test on the tank now. Just had to add it to the websockets but now it seems like the new debugging seems to be working.

#### 09:30 | 1.5 hours

Found this website for RTK: `https://macors.massdot.state.ma.us/`. Seems like it will work pretty good in Massachusetts, but will need to find a new one when not in state.

Made some really good progress on getting RTK GPS working. There is a 40% chance that the only thing I need to do to get it working now it to bring it outside so that it can get a level 4 fix.

#### 19:00 | 1 hour

Have been having some fun time with RTK. Ended up getting something working with `rtk2go.com` but have still not gotten an RTK lock...

### Tuesday, May 5th | 1 hour

#### 18:30 | 1 hour

Here is some data that I got from the GPS. It is a `UBXMessage`: `<NMEA(GLGSV, numMsg=3, msgNum=1, numSV=9, svid_01=68, elv_01=26, az_01=46, cno_01=, svid_02=69, elv_02=66, az_02=352, cno_02=, svid_03=70, elv_03=39, az_03=262, cno_03=, svid_04=77, elv_04=4, az_04=11, cno_04=, signalID=)>`

Another type: `<UBX(NAV-PVT, iTOW=22:42:33, year=2026, month=5, day=5, hour=22, min=42, second=33, validDate=1, validTime=1, fullyResolved=1, validMag=0, tAcc=3, nano=-76042, fixType=3, gnssFixOk=1, diffSoln=0, psmState=0, headVehValid=0, carrSoln=0, confirmedAvai=1, confirmedDate=1, confirmedTime=1, numSV=22, lon=-71.1720552, lat=42.370101, height=8567, hMSL=41733, hAcc=750, vAcc=970, velN=-6, velE=39, velD=9, gSpeed=40, headMot=207.72908, sAcc=131, headAcc=52.49496, pDOP=1.23, invalidLlh=0, lastCorrectionAge=0, authTime=0, nmaFixStatus=0, reserved0=843696860, headVeh=0.0, magDec=0.0, magAcc=0.0)>`

I am pretty sure we want fix type 4 because that is RTK.

Done for now. It isn't working, I think we are making progress though. Not sure if the GPS isn't accepting the corrections, or if we aren't getting them from the server. Action points for next time will be:

- Try to print data we are getting from caster
- Somehow ensure they are being sent to the GPS and read by the GPS

### Friday, May 8th | 1.7 hours

#### 16:20 | 1.7 hours

Going to start by getting the cell modem all set up, then doing some RTK testing, then going to do more field testing!!

Added the modem. Now going to see if it worked. Used this command to add it: `sudo nmcli connection add type ethernet ifname usb0` also make sure to give it a lower route than wifi: `sudo nmcli connection modify usb0 ipv4.route-metric 50`, and check everything with these commands: `nmcli device` and `ip route`

Now that the modem is working, I am going to see if I can get RTK GPS working now that we have better networking!

FIELD NOTES:

- Still uses WIFI for stuff when in field
- Controller keybinds
- Add video to self driving
- Boomerang at waypoint
  - Use PD or PID?
- Show map of where tank is and where waypoints are and what one it is going to

### Saturday, May 9th | 1 hour

#### 13:00 | 1 hour

Started by adding everything from my field test notes into my task list and ordering it. Going to start today by trying to get RTK GPS working. As much as I want to get this working, irdk if it is worth all the time... Because I want it to work even if RTK isn't an option or there isn't any internet... I don't know, I think if I can't make any more progress today, I should stop working on that part...

GOT RTK GPS WORKING!!! It is only in float mode right now, but I think that is fine because it can only see around half the sky right now. Am going to now take the working code and rewrite the GPS library.

Ended up spending some more time getting the RTK GPS working with live location. So didn't rewrite the library, will do that next time.

### Sunday, May 10th | 1.5 hours

#### 16:30 | 1.5 hours

Going to start by taking the working code for the existing RTK testing, and replacing the GPS library with that.
Done rewriting library, going to test. Then going to start working on the website more, I think I might just keep the same theme for the self driving page, but make it so you can scroll to see all the info... Not sure though, I do like the idea of having all the data on one screen.

Got controller bindings working so that some buttons flick switches. Took a while because I had to deal with debouncing (I think thats the right term). Going to start looking into how to get the map on the self driving screen. Just got a good idea, we should make the camera have an option to instead show the map there. Lowk I don't even know if we need the tabs at the top... Might make sense to put it all on one tab? I don't know though, maybe just combine self driving and route planner.

Thinking about a new UI so that we don't need to split everything into tabs. But not sure how to fit everything into once screen. Might change anti doxx so that it is on by default but if you click on the GPS coords it turns off.

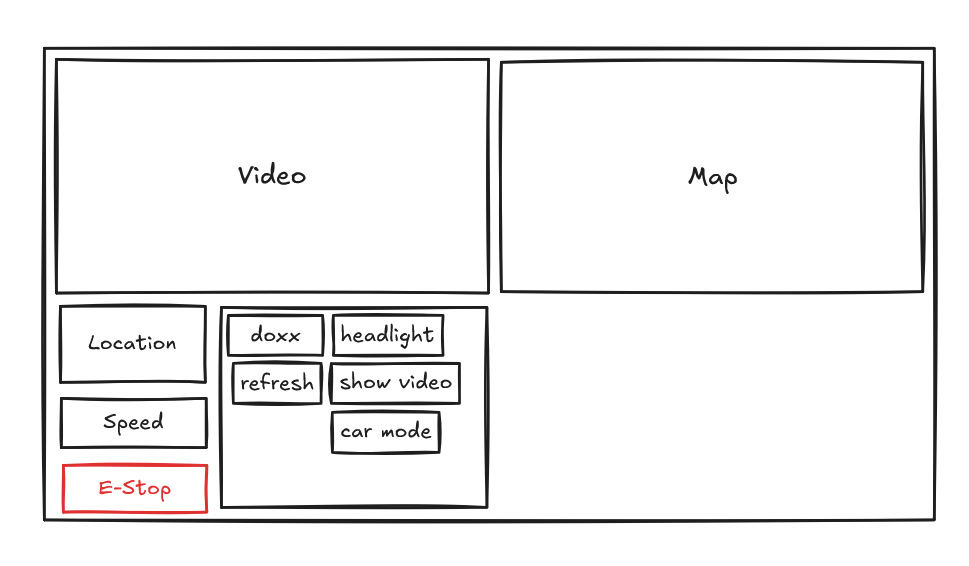
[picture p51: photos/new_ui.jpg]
New UI outline


### Thursday, May 14th | .5 hours

#### 17:50 | .5 hours

Going to start by making a static version of the new UI that I want to make. Once I have the static version looking nice, then I will wire up all the different parts and deal with all the bugs.

Started on the new page, have a decent idea of how I want it to look, now just need to add the map, design buttons, and design telemetry section.

### Friday, May 15th | .66 hours

#### 19:30 | .66 hours

Going to continue workoing on the UI tonight. Hoping to finish the new UI tomorrow morning and get RTK working for NH so that we can do some testing.

Have been thinking, and we should make sure that the main page doesn't have too much logic, it should just be calling a bunch of components. So once I get the map working, I am going to redo the camera.

Got the map working! Now going to redo the camera and maybe redo the div layout because I kinda made it complicated...

### Saturday, May 16th | 1 hour

#### 11:00 | 1 hour

Going to start by finishing the new UI. Then making sure everything works, because I think it will need a few logic changes to make sure that everything is working.

I really don't know how I feel about the anti doxx thing. Like I wish I could just show the coords, but I don't want to be doing that when at my house... Whatever...

### Sunday, May 17th | 3 hours

#### 13:00 | 1 hour

Worked on getting all the settings working. I think I have them all up and running. Next I am going to make the new file that will handle all the controller logic. Once that is working, I _think_ the new UI will be all up and running. It won't have every metric yet but its enough for testing.

#### 17:00 | 2 hours

Going to start on the controller stuff for the new UI. The code itself isn't new, but just figuring out how to link it all is...

The new site is connecting!! Going to fix all the bugs, then once it seems to be working as it was last week, I am going to bring it in the charge, and while it's doing that, I am going to make a few UI changes.

Things to fix:

- [x] Ping
- [x] Headlights (Don't know what I did to fix this)
- [x] Not using correct controller bindings?

UI things to fix:

- [x] Make everything fit so that it doesn't scroll
- [x] Make video 480p again so no black bars
- [x] Add self driving button
- [x] Show tank position on map

Think I got everything working. Going to reboot to make sure motors are working, then charge the battery while I do some small UI changes and add the self driving button.

FIELD TEST NOTES:

- Site doesn't work on ally
- Still have wifi issue...
- Don't see tank on map
- Motor dual command issues

The site wasn't working on the ally because I needed to accept the bad website. It wasn't loading becuase it was trying to go to http by default when the correct prefix is https. Now that I think about it, I don't think the WiFi was the issue, I think it was the motor issue that just happened when I was far away. Next issue is that the tank dot doesn't show on the map. Not sure why but I assume it has something to do with not being a reactive element. Last issue is that the motors were crashing again. I think the issue is that two things are trying to command them causing the serial port to crap out. The true solution is to add a lock so that only one command can be set at a time, but I think the main thing causing this to happen more often is because I haven't updated any of the code for the new UI. This means that it was sending commands from the joysticks even though it was also trying to self drive at the same time.

### Tuesday, May 19th | 1.5 hours

#### 08:30 | 1.5 hours

- [ ] Fix UI on site
  - [x] Add correct border and spacing to video
  - [x] Create new button UI
  - [ ] Add more stats
    - [ ] GPS Telemetry
    - [ ] Heading
- [ ] Fix tank location on map
- [ ] Motor issues
  - [ ] Make sure website isn't sending commands while self driving
  - [ ] Add a lock to motor driver

Going to start by working on getting the video CSS working on the site.

Fixed the video UI. Now going to figure out if I want to make a smaller button UI, and if I do, then how I will make it look. Decided to just keep the current style and just change how the icons look, because CSS is giving me a headache.

Made a new UI for the buttons, so now they are square to match the rest of the theme and change color when they are toggled. Going to change how they are aligned, then start reworking the telemetry section.

Done realigning the settings section. Now going to redo the telemetry section. I think I am going to make a section that has all the GPS info, and everything else can stay as is.

Started on the new GPS telemetry section. Also need to find a spot to store the compass data that we are getting... But before I can even do that I need to add something that reads this from the websockets and adds it to stores.

Next steps:

- Read new telemetry from WS
  - GPS
  - Compass
- Design UI for new telemetry

### Wednesday, May 20th | 1.5 hours

#### 09:30 | 1.5 hours

- [ ] Fix UI on site
  - [x] Add correct border and spacing to video
  - [x] Create new button UI
  - [ ] Add more stats
    - [x] GPS Telemetry
    - [x] Heading
  - [x] Fix video CSS when connected
  - [x] Fix button offset on IP screen
  - [x] New anti doxx
    - [x] Make it so you just need to click on it to show
- [x] Fix tank location on map
- [ ] Motor issues
  - [ ] Make sure website isn't sending commands while self driving
  - [ ] Add a lock to motor driver

Going to start today by adding the logic that will take the new telemetry and save it to stores. Then will make the new UI to display it!

Added all the new telemetry and also fixed the issue with video CSS that happens when you actually connect the video. Now going to fix a small visual bug on the IP picking screen and then make the new anti doxx version.

Done with the new anti doxx! I like it a lot more and now it doesn't take up an entire switch. This means we are done with all the UI changes I wanted to make! Now going to figure out why the tank location isn't updating.

Done making the tank location show on the map! Just had to make some things reactive! Done for now! Next time I want a fun project for the website I should make it show what waypoint it is going to. Not going to do that right now though... Next thing I need to do before we are ready for a field test is to fix the motors and it should be ready for the waypoint only ship on Saturday!

#### 18:30 | .33 hours

Changed the map to use the location it gets from the tank instead of the users location. Is much faster and would be useful if you are controlling the tank from far away. There is probably a way to make the browser location faster, but this is better anyways.

### Sunday, May 24th | 2 hours

#### 19:00 | 2 hours

- [x] Fix WebRTC using WiFi instead of modem
- [x] Add camera mount
- [x] Motor issues
  - [x] Make sure website isn't sending commands while self driving
  - [x] Add a lock to motor driver
- [x] Figure out why tank mode isn't working
- [x] Change self driving buttons to a switch

Tonight I am going to finish up the waypoint version. That means adding all the final touches so I can ship waypoints. We are not stopping though. Now that waypoints are working, we are at the point where we can start adding more advanced AI / ML. Not sure if any of the ESC things will get fixed... Depends on if I remember how to program them.

Vibe coded some code that should make it so that when WebRTC finds a link it doesn't use wifi. Hopefully it works. Also just added some camera mounts to the frame. One in front and one in back. Hopfully I can get some cool videos with it tonight. Now going to start debugging the website.

Now that I am reading the code, _I think_ that I commented out all the stuff that actually does stuff, but there are a few other vars I need to get rid of. Then it should just be, if self driving, don't send gamepad inputs.

New motor fix seems to be working. Now there is only one thread that is controlling it and everything goes through it. Now going to add some code on the website so that it won't send gamepad commands when in self driving mode. Thought I fixed it, but now it is only saying waypoint mode for a second before going back to normal...

Got all the motor issues fixed. Just spent 30 minutes figuring out why it wasn't working, but I was checking if the status was `Self Driving`, when I meant to check if it was `Waypoint Mode`. `Self Driving` isn't a mode... Now I need to figure out why it is stuck in car mode.

Fixed tank mode, also turned self driving mode into a switch and added a button on the controller for it. Going to call it a night for now. Hopfully I can finish the other features in the morning, and ship the waypoint version. Also hope to start doing ML tmr!!

### Monday, May 25th | 4.39 hours

- [x] Export / import waypoints
- [x] Fix ESC issues
  - [x] Turn off timeout
  - [x] Slow down faster on timeout (depends on how the code handles it... if this would make it go slower when sending normal cmds don't change it)
  - [x] Higher Buadrate? (Again, if this breaks things, turn it off)
- [x] Tighten screws on bottom
- [ ] Fix waypoint turning code
  - [ ] Make it PD or PID
- [ ] Add a bunch of pictures to this journal (its been a bit bland)

#### 16:00 | 1.33 hours

Going to start by making it so that you can import and export waypoints. Just going to export them as a CSV file. Got downloading working. Now going to get uploading working!

Got uploading routes working!!! Was a bit hard but now it works!! Now going to look in the code for the hoverboard and see if I can even find the code that I need to change to do what I want. If I can't find it now, then I'm just going to skip it.

#### 18:00 | 1.33 hours

Looking at the ESC code to see if I can find the options I need. If I end up fixing all the issues, getting BLDC_SIDE working would be nice. Also using revs/s\*1024 might be useful. Not sure really... The current speeds are fine and everything should be reactive anyways. I really don't want to open this can of worms, so I might just quit trying to ever fix these ESC issues. They aren't super bad anyways.

Found all the settings, now that I think about this, it is going to be a pain to test the changes because it _should_ not happen via the default software.

Changed `SetFilter(14);` to 10, we will see if that makes a difference.
Changed `#define INACTIVITY_TIMEOUT 8` to 300, so that should be fixed.
Changed `#define REMOTE_BAUD 4800` to 19200.

Now going to see if I can figure out how to program this john.

Done reprograming the ESC's. Now going to see what I broke. First need to change the baud rate in the python code.

I fear the higher baudrate broke some stuff. I don't even remember why I had it on my list of things to change. I think I thought it was causing the issues that were from reading the serial without a lock... Going to try 9600 but if I see anything weird I am going back to 4800. Also need to test the slow down speed, just going to unplug the cable to test that.

9600 is a lot better, but once I test the other stuff, I am going to test a 4800 and see if it looks better, becuase I think there might have been a reason for using that. Seems like I fixed the slow down issue!! Now just going to test 4800 and I think I am done!

Yep, 4800 baud is much better. But good that I found where everything is! Now going to go fix some physical things, then do the test drive, tune the P or make it PID, and get the video for shipping!!

#### 20:00 | 1.73 hours

Have been messing with PID, I made a graph of what it is doing, and it doesn't look like it will need PID, I just need to figure out why the data isn't updating...

Wasn't able to fix the GPS issue. That is the last thing I am going to work on before starting AI.

Here is a chart of the goal heading (blue, calculated using current position and goal position), and current heading (red). This explained a lot of the issues I was seeing in waypoint mode (or my data taking method is broken), as you can see, once it is told what heading to go to, it does it decently, sure it could be better, but it isn't the main issue. The main issue is that the goal heading isn't updating much at all (it should be updating more than once a second, this data is from around 20s). It seems like this issue is steming from the GPS driver. So the next step is going to be use the test script and see if that one is actually updating the data at the right rate, then once that is, then figure out why the driver is not.

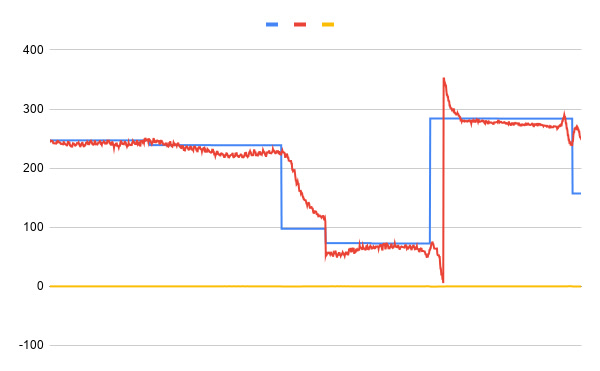
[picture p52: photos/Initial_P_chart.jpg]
Initial P tune


PHOTO DUMP!!

Tank in field Tank on workbench Tank on road Tank with camera mounts Early version of new site on ally

### Tuesday, May 26th | .66 hours

#### 17:30 | .66 hours

Going to spend this time writing the ship for version 3 (waypoints). Even though I am shipping it now, I am going to work on one more big waypoint bug after this, then start on version 3.5 (ML self driving). That version will add the cool stuff like staying on sidewalk, although not sure how much of that is going to get done, and or if I am going to keep working on this project throughout the summer. Don't get me wrong, I _love_ this project, but sometimes a change is good. Or a project is just done for now. I can always come back to it later!

### Saturday, May 30th | 4 hours

#### 14:15 | 2.33 hours

Going to start today by figuring out the issue with the desired heading not updating enough. Assuming it is because the GPS is not updating enough. Once we have this fixed, hoping to start working on getting some ML working. I really have no idea how ML is going to work, all I knew was that waypoints had to go first, so I am hoping it can just fit in, but idkkkk.

Having issues with the tank getting cell service :sk:. Trying to see what I can do to get it on cell... It would work on WiFi but then it is going to be a pain to test the waypoints. Going to see if I can find a better antenna to use... Ended up just bringing it inside and using WiFi, but this is going to be an issue once I am ready to test waypoints. First going to get RTK working using that same trial I used last time, I think it should be fine.

Going to start debugging this by ploting the data that is coming out of the testing script and see if it looks like it is updating enough. If it is, then will add same statement to real code and see what's happening.

On `rtk_gps_test.py` it _seems_ to be updating with each print statement... There is a small chance that it is just moving a small number and won't reflect big changes, but I think it is good. Going to add the same debug to the real program and see if there is a difference.

The GPS in the real program is def updating a lot less than the script. Now going to see if I can find a difference. The only difference I see is `sleep(.1)`, which sure, adds time, but not a second of time... Anyways, going to test without it now. Weird, removing that seemed to fix it... Not sure why though because it changed it from being like over a second between updates, to many times per second. Now going to see if I can figure out this cell service so that I can test this. Actually, should be able to test just holding the tank. Going to do that first. Really not sure why it doesn't have cell though, it is only 1 bar here, but that should be enough to at least connect to. Might see if I can debug that next, although I am not sure I am going to learn anything new. I think it will just say that it isn't finding a tower.

Note for future self: Remember that you made it so that video does not work over Wifi, if you want it to work when testing inside you need to turn that off. Haven't testing the self driving yet, but heading def changes a bit when the wheels are spinning... Not sure if it is enough to cause an issue though... Should also add an offline mode, although I don't know how much work that is going to take.

I think I that fixed the issue? Going to see if I can get cell working bc I really don't wanna stand outside to test this rn. Think I'm just gonna put my phone in the tank and it will use phones network.

Fixed the issue! Now going to add some PID and try to tune it a bit.

#### 19:00 | 1.66 hours

Starting to tune the PID loop. Should be done with this tonight, take a video for shipping it, and be ready to start on ML in the morning.

Have just been working on tuning the PID look but the GPS seems to have shit itself. No idea why but it lock RTK lock and now has 800m accuracy... Need to fix this before I keep tuning it. Found the issue... Somehow the SMA connector for the GPS antenna came undone. Not really sure how that happens but ok I guess. Back to figuring out this PID.

I think I have a decent tune for the PID now? It is only KP, but there seem to be some other issues also... I'm just going to end today by recording a demo video. Then tmr am going to start figuring out how we are going to add ML. I will probably do some more waypoint tests once back in Boston because there are a lot of issues right now... Cell isn't working bc of location, uhh yea that is causing a lot of issues. Might also be something with the compass? Not really sure. Anyways, yeah, video today, start on ML tmr, go back and do some final PID tests once back in town.

I am so stupid. When tuning the PID loop, I was reading the values from a .env file, but I forgot that I run `load_dotenv()` at the beginning of the file, so I never reloaded it. That meant that the values it was using only changed when I reloaded the entire program. Good news is that a tune of 1, 0, 0 seems good enough for now. Got the videos I need for shipping, so going to edit that then call it enough for today.

Just shipped and got aproved for horizons. Right now it is at 108 hours on hackatime, and I shipped 74 hours. So everything on from hour 108 is new and can be used for a new program.

## **VERSION 4**

This version is around adding ML features to the waypoint mode, really turning it into a self driving car instead of a point following car. Not sure how much is going to get done (see above) but the idea right now is to have a setting that keeps it on sidewalks, while still following waypoints the best it can.

It also includes a new frame! Here is a list of things the frame should have:

- Suspension
  - Be able to go offroad
- Good turning radius
  - Crab / front and back turning?
- Waterproof (like a real car)
- Trailer hitch
- Spot for E-Stop
- Laptop charger / USB PD out
  - Maybe also do PD in for charging main pack
- Attachment spot
  - Laptop holder
  - Include power and a data line
- Lights:
  - Good headlights
  - Brake lights?
  - Blinkers?
  - Maybe just a lot of neo pixels for this...
- Pack into suitcase?
  - 62 linear inches is normal for checked luggage, so aim for that
  - ^ is the total case, so figure out if it will be mailed itself, or in something
  - maybe make it fit in this? https://www.pelican.com/us/en/product/cases/1615?sku=016150-0011-110
  - Should make a fake frame out of wood to get idea of size I am working with

### Sunday, May 31st | .5 hours

#### 10:30 | .5 hours

Now that we have waypoints working, I'm kinda going to change directions and work on a solely ML mode that just follows a person. I want to learn the basics of ML on the Jetson before we add it into the existing waypoint mode.

Going to start by adding a button for ML mode to the site (this will be temp while we are testing) then getting the code on the tank ready to handle two different self driving modes.

Think I have a decent outline for ML mode in the website and tank code. Now waiting for everything to download...

### Monday, June 1st | 1 hour

#### 17:30 | 1 hour

Aiming for just 1 hour of some light work today. Going to start by getting coolify linked with GitHub so that the deployments are shown instead of the old vercel stuff. Then going to probably just try to figure out how this ML works. Again, the goal for now is to follow a person so that I can kinda just learn about ML, then we will later integrate more ML into the waypoint mode. Not sure what the first thing I'm going to add to waypoints, but this is kinda also figuring that out.

ALSO, WE GOT SPONSORED BY RTKDATA! Not with any money yet, but they said they would be willing to give me a free RTK plan if I could take some data and they could add it to their website. So at some point soon I just should start logging all the gps data, just so that I have it. I will figure out the graphing and all that later, but I just need it logged. Ahhh coolify seems to have gone down, going to need to fix that. Hosted sites seem to be fine, so not the end of the world yet, but this needs to be fixed.

Might have fixed coolify? Pushing to test. It worked!! This took way too long, but at least it is done. It has been a small thing that has been bugging me for a while.

Starting to figure out what code I need to be running. As you can see, I have no idea what I am doing with ML / AI.

### Tuesday, June 2nd | .4 hours

#### 11:00 | .4 hours

Going to start working on adding some logging for the RTK data. Just done with MCAS so I'm only really going to have around 30 minutes to get it done now, but that _should_ be enough time.

Think I have a basic logger working. Need to first check if it works, then make sure that it is logging all the data that I was told to log in the email.

### Tuesday, June 23th | 2.33 hours

#### 16:00 | 2 hours

I think I have decided that I am going to keep working on this project throughout the summer. Not 100% sure, but pretty sure. If I do, going to start by finishing adding all the RTK logging and starting on using ML to help it drive. Then going to get started on working on the frame so that parts can arrive while I'm on vacation.

Going to try and finish up getting the RTK logging working. Going to start by making something that times how long it takes to get to fixed. Then need to make something that figures out distance from base station.

Before I work on logging today, I am going to take some measurements of the current tank and do some recearch to figure out the size I want the new one to be.

Current body size: 55 x 30 x 10 cm
Current with wheels: 55 x 60 x 20 cm

Max size in [1615 Air Case](https://www.pelican.com/us/en/product/cases/1615?sku=016150-0011-110#specs): 75.16 x 39.37 x 23.83 cm

Idea for new body size: 70 x 30 x 15 cm. This is going to the be main part that has to go in the box. Everything else should come apart to lower the size. Hoping for the inside of the tank to have 10cm usable room. Now going to look up similar tihngs to find how I should make it.

Have been drawing out a simple design, and I'm not really sure how to get the proportions I want while keeping it in a size that it able to be checked on an airplane. I think it should be portable, but still a respectable size. Now that I look at it more, the main body should fit fine, I just need to lower the wheels a bit to get the height that I want. I think it will really start to make more sense once I am designing it. Looked at calendar, and if I want to bring this to outpost (if I can go), then I really need to start on the new frame ASAP. Plan right now is to get logging done today, then tomorrow and Thursday get follow mode working. Once follow mode is done, I am ready to do the new frame.

Apparently, they never gave me the free RTK connection, so I now have to go back to MACors for now and email them. I think I got all the logging done. Only issue is that the the saved log is kinda a mess, so I am going to write a quick script that will read the full log and just take the data that I want, in this case, the time to lock data. Then going to have it output it in a form that is easy to visualize. I think just a copy paste csv is a good idea.

I was about to write some quick code so you can see the lock time code on the website, but now it is deciding to loose cell... I can't tell if it is loosing cell, if it is somehow on WiFi and loosing that, or if this is a power issue. For now I am just going to bring it inside, but once I bring it out to the field it would be a good time to test wtf is wrong. Lights seem to not be working... Going to debug that, then the power / internet issue. I have the bare minimum done for logging, so after today I am not going to work on it, but if I have time tonight, I might add a chart to the website (not likely). No idea why lights aren't working. I guess that is something to work on next time.

#### 19:40 | .33 hours

Not really sure why the lights are not working, but not going to debug it now because I don't have the right tools. Going to work on finishing that logging tool I wanted to add to the website.

Just finished making a _really_ quick script that just reads through the log file and prints all time to fixes that the tank has had.

### Thursday, June 25th | 2.8 hours

#### 10:30 | .8 hours

Going to start today by figuring out why the lights aren't working and why it seems to be loosing power or internet. First going to deal with lights.

Seems like nothing is being sent out of the pin for the lights.

For some reason SPI1 was turned off in jetson-io. I have no idea how it got turned off, as I haven't been messing with that stuff in ages, and I also have no idea why it is now called SPI1, but lights works now!

Just turned off the WiFi chip entierly because it is being a pain.

Need to stop now, but next thing to do today is to check if the GPS locking is getting logged correctly and then also have the log reader print the location where it locked at

#### 18:00 | 2 hours

I think the issue that seems like network loss is that when it is on a really weak cell link, and then you start streaming video the link gets saturated and can't keep up. Going to try again but turning video off. For some reason it isn't getting a lock right now. Going to try switching to MaCORS and see if that is any better. Wait, it might get a lock just take a bit...

Even in a really good spot I am only getting RTK float... Might try going back RTKdata to see if that is any better but idk why this is happening.

UGHHH did a test run and like 20 things broke. I lowk don't know if I want to fix then before doing the new frame because half of the issues will be gone with the new frame anyways. So I think I might just call it quits on this frame for now. I did a good run, and I really don't feel like fixing issues on a frame that is about to be retired anyways... It had a really good run, but it's just time to replace it.

Issues:

- Won't drive to follow waypoints
- Right wheel stops working
- Make map follow robot

Going to start by making the map follow the robot, but then after that, I am fully switching to the new frame. Like even if I will still have the self driving issue on the new frame, I would rather fix it on the final device...

Kinda vibe coded a fix but it should be fine. Now going to start getting the basics set up in fusion. Like getting all the sizes I need.

### Saturday, June 27th | 1.33 hours

#### 17:30 | 1.33 hours

Working on learning how to use extrusions in fusion. It is really confusing but I hope once I figure it out I will know enough to design the frame...

Got a nice simple rectangle working! Now need to start thinking about how I want this thing to look. I have a very rough outline, but other than that all I know is I want a nice metal frame lol.

Rectangle Frame V4

### Sunday, June 28th | 1.66 hours

#### 16:30 | 1 hour

Not sure if I like how the hardware that holds the rectangle together is on the top. I might want the top flush so that it can have attachments or things that can take advantage of the full width. Going to start today by working on moving that hardware to sides and then finishing the outline of the rest of the core frame. Might also add the plastic that I want to use for this part... Lowk I think I might just use sheet metal for the walls as it doesn't look like it will cost much more and idt it will add much weight. Just so I don't forget, I am going to use [this](https://www.homedepot.com/p/Falken-Design-24-in-x-60-in-x-1-8-in-Thick-Aluminum-Composite-ACM-Black-Sheet-Falken-Design-ACM-BK-1-8-2460/308670306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).

Made some good progress. Ended up switching to internal joints and also did some drawing to figure out if the real version will look good. By real I mean the version that will work due to minimum sizes. Now going to start on the ends, which are going to be 10cm tall, then making the 45 degree angle peice until it is the full 20cm.

Chassis V4 with internal joints

#### 17:30 | .66 hours

Started working on the shorter front. I haven't been doing any joints, but it shouldn't be too bad because it is all going to be joint in place. So I am just going to do all those either once I am done figuring out the overall geometry or once I remember again lol. Here is a nice picture.

Short front on frame V4

### Monday, June 29th | .66 hours

#### 09:00 | .33 hours

Started today by making that custom mount / joint thing. Hopefully once I am done with the overall frame and adding the metal walls it doesn't get in the way. Like it will, but I hope it is easy to move it after the fact. Now going to add the screws and things and then do it for all sides.

Custom 100mm joint

#### 10:00 | .33 hours

Done for now. Added some screws, but having a lot of issues with this last screw...

Stupid screws

### Friday, July 3rd | 1.5 hours

#### 17:00 | 1.5 hours

Today I am going to be working on getting the rest of the shape of the frame built out! I can not figure out why this frame wants to move out whenever I make a joint for the life of me...

Needed to do a bunch of grounding to get it working. Now working on figuring out the geometry so that it looks good while being possable to build.

Very rough area needed for outside metal: 3,280 cm^2
Area in [this](https://www.homedepot.com/p/Falken-Design-24-in-x-60-in-x-1-8-in-Thick-Aluminum-Composite-ACM-Black-Sheet-Falken-Design-ACM-BK-1-8-2460/308670306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) piece of metal: 9,120 cm^2

Wow, actually using trig in real life now. Going to start on the 45 degree stuff tomorrow.

V4 frame with the short parts now on all sides

### Saturday, July 4th | 3.32 hours

#### 11:30 | .6 hours

My goal for today is to finish the core frame and then figure out how I want the shell to work. The two options are inside or outside. I think outside is easier, but then the question is how can I mount things on the outside. Although I don't think I will be needing to mount much on the outside other than the top. So the top is its own issue. Was talking about batteries and I might want a door on the bottom to switch the battery pack... Will start spacing that all out once the frame is done though (am making a 18650 pack from scratch). Might wanna figure out wheels first though...

Ended up taking a bit of time to get my 3d printer working, then started on the 45 degree angle cuts.

#### 12:30 | 1 hour

Am thinking about if I want the metal on the outside or inside, and the two main things are that I need an attachment point for things on top, and I might want a trailer hitch. And maybe more cameras. I guess what I'm saying is that I want to still be able to attach things to the outside even with the metal.

Waitttt, I didn't know you could put metal or plastic in the middle using the groves. I might do that. It will make the top a bit more interesting, but it might be better. I am going to finish just getting the frame done though, and then I can kinda redo the whole top. It is annoying that I spent all this time on it, but it isn't too bad, I was learning.

#### 14:00 | 1.66 hours

Got the 45 degree angle stuff sorted out, now going to work on the connectors and cross beams.

Started on the cross beams, but ended up getting stuck on removing past parts. Really not able to think right now so I am going to try and figure this out tomorrow.

### Sunday, July 5th | 4.5 hours

#### 11:30 | 2 hours

Going to start today by figuring out this error I made by removing past pieces. Then going to finish adding the crossbars and start adding the plating.

FIXED IT IN 10 MINUTES. I SWEAR I JUST NEED TO TAKE MORE BREAKS. Now going to add crossbars, and then make these plates and see how much it is going to cost me.

Just realized that if I use these internal joints, then I won't be able to add plating, so I think I am going to use external surface joints? Not sure yet, I am now trying to remember why I stopped using those for the side. I think it was just that there was a simpler way to do it. I don't think I am going to be mounting much on the bottom, and def not on the corner so I think it should be fine. Also should start thinking about if I want a door on the bottom to take out the battery... I think that might be too much work, like I think I will just try to design the top to make it easy to get to the bottom and battery, but the point is that it should be a big enough battery that it doesn't need to be changed constantly. For now I am just going to use external joints, and we will see if it becomes and issue.

Made some good progress and am almost done making the first metal plate, just making sure that this AI is not making things up before I do it lol.

#### 17:00 | 2.5 hours

Going to try and work on this for 2 more hours today. First going to finish checking these measurements on the gasket that I am going to use, then make and price out all the plates for the tank. No offense to anyone Chinese, but trying to understand bad Chinese english is a skill of its own.

Sendcutsend is looking a bit exspensive so I think once the design is done I am just going to give them the parts that are too complicated / I just don't want to cut myself, and everything else I will do myself. Going to try and finish the blank panels today, and then tomorrow I think I am going to start on the steering and wheels and suspention and all that. The final thing will be adding all the stuff to the inside / adding any holes I need to the plates.

WHY WILL HOME DEPOT NOT SELL ME METAL COLORED METAL??? Anyways, did some simple maths and for a piece that is almost certintly going to be the same in the final design and is just a plain rectangle SCS wants $36 and if I buy from Home Depot and cut myself it will cost $5. I think I am going to use SCS for the side pieces and probably the bent ones unless something else gets super hard.

Done with the bent panels. Not sure what I am going to do for the top yet, all I know is that I will need a opening to get inside, and probably spots for cables / SMA connectors to leave. Because now that the frame is metal, we can't have any antennas on the inside. I think I am going to leave that to the end though. Second big thing I need to do is to figure out the steering system.

The new frame with all the panels added

### Monday, July 6th | 1 hour

#### 18:00 | 1 hour

Going to start today by figuring out how to do the wheels. I really have no idea where to start.

These wheels are going to be a freaking pain in the rear to figure out. I'm having a hard time even finding MOA (motor on axle) axles in the first place. Not even checking if they are the right size yet... AHHHH.

I think I am going to end up making my own thing from scratch for this. I hope it isn't too much work and that it doesn't cost too much.

### Tuesday, July 7th | 2 hours
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

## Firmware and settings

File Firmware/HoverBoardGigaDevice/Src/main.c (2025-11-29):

#define ARM_MATH_CM3


#include "../Inc/defines.h"
#include "../Inc/it.h"
#include "../Inc/bldc.h"
#include "../Inc/commsMasterSlave.h"

//#include "../Inc/commsSteering.h"

//#include "../Inc/commsBluetooth.h"
#include "stdio.h"
#include "stdlib.h"
#include "string.h"
#include <math.h>     
//#include "arm_math.h" 
#ifdef IMU_ENABLE
	#include "../Inc/mpu6050.h"
	extern ErrStatus    mpuStatus;                  // holds the MPU-6050 status: SUCCESS or ERROR
#endif


#ifdef BUZZER
	extern uint8_t buzzerFreq;    						// global variable for the buzzer pitch. can be 1, 2, 3, 4, 5, 6, 7...
	extern uint8_t buzzerPattern; 						// global variable for the buzzer pattern. can be 1, 2, 3, 4, 5, 6, 7...
#endif


#ifndef STAND_STILL_THRESHOLD // Posible to override in config.h or define_*.h
#define STAND_STILL_THRESHOLD 50
#endif

uint8_t iDrivingMode = DRIVING_MODE;	//  0=pwm, 1=speed in revs*1024, (not yet: 3=torque, 4=iOdometer)
uint8_t bRemoteTimeout = 0; 	// any Remote can set this to 1 to disable motor (with soft brake)
uint8_t bPilotTimeout = 0;	// any Pilot can set this to 1 to disable motor (with soft brake)
uint32_t iBug = 0;
uint8_t iBug8 = -1;
uint32_t steerCounter = 0;								// Steer counter for setting update rate
int32_t speed = 0; 												// global variable for speed.    -1000 to 1000
int32_t speedShutoff = 0;
int16_t speedLimit = 1000;


#define STATE_LedGreen 1	
#define STATE_LedOrange 2	
#define STATE_LedRed 4	
#define STATE_LedUp 8
#define STATE_LedDown 16
#define STATE_LedBattLevel 32
#define STATE_Disable 64
#define STATE_Shutoff 128

uint8_t  wState = STATE_LedBattLevel;   // 1=ledGreen, 2=ledOrange, 4=ledRed, 8=ledUp, 16=ledDown   , 32=Battery3Led, 64=Disable, 128=ShutOff
uint8_t  wStateSlave = STATE_LedBattLevel;   // 1=ledGreen, 2=ledOrange, 4=ledRed, 8=ledUp, 16=ledDown   , 32=Battery3Led, 64=Disable, 128=ShutOff

#ifdef MASTER_OR_SLAVE
	DataSlave oDataSlave;
#endif

int32_t ShutOff(void);

#ifdef MASTER_OR_SINGLE

int32_t steer = 0; 												// global variable for steering. -1000 to 1000
FlagStatus activateWeakening = RESET;			// global variable for weakening
FlagStatus beepsBackwards = SET;  			// global variable for beeps backwards
			
extern uint8_t failsafe_status;
			
extern float batteryVoltage; 							// global variable for battery voltage
extern float currentDC; 									// global variable for current dc
extern float realSpeed; 									// global variable for real Speed
uint8_t slaveError = 0;										// global variable for slave error
	

#ifndef REMOTE_AUTODETECT

extern FlagStatus timedOut;								// Timeoutvariable set by timeout timer

uint32_t inactivity_timeout_counter = 0;	// Inactivity counter

void ShowBatteryState(int8_t iLevel);

	const float lookUpTableAngle[181] =  
	{ -1, -0.937202577, -0.878193767, -0.822607884, -0.770124422, -0.720461266, -0.673369096, -0.628626737, -0.58603728, -0.545424828, -0.506631749, -0.46951635, -0.433950895, -0.399819915, -0.367018754, -0.335452314, -0.30503398, -0.275684674, -0.24733204, -0.219909731, -0.193356783, -0.167617063, -0.142638788, -0.118374098, -0.094778672, -0.071811398, -0.049434068, -0.027611115, -0.006309372, 0.014502141, 0.03485241, 0.054768601, 0.074276213, 0.093399224, 0.112160212, 0.130580478, 0.148680146, 0.166478264, 0.183992885, 0.201241154, 0.218239378, 0.235003093, 0.251547129, 0.267885663, 0.284032276, 0.3, 0.315801365, 0.331448439, 0.34695287, 0.362325923, 0.377578512, 0.392721236, 0.407764409, 0.422718089, 0.437592106, 0.45239609, 0.467139493, 0.48183162, 0.496481645, 0.511098642, 0.5256916, 0.540269454, 0.554841097, 0.569415411, 0.584001283, 0.598607627, 0.613243408, 0.627917665, 0.642639528, 0.657418247, 0.672263213, 0.687183982, 0.702190301, 0.717292134, 0.732499689, 0.747823448, 0.763274197, 0.778863056, 0.794601516, 0.810501473, 0.826575268, 0.842835728, 0.859296209, 0.875970644, 0.892873598, 0.910020317, 0.927426794, 0.94510983, 0.963087109, 0.981377271, 1, 1.018976116, 1.038327677, 1.058078086, 1.07825222, 1.098876565, 1.119979359, 1.141590767, 1.163743061, 1.186470823, 1.209811179, 1.23380405, 1.258492439, 1.283922754, 1.310145166, 1.33721402, 1.365188293, 1.394132116, 1.42411537, 1.455214362, 1.487512601, 1.521101681, 1.556082309, 1.592565485, 1.630673867, 1.670543366, 1.712325006, 1.7561871, 1.802317825, 1.85092826, 1.902255998, 1.956569473, 2.014173151, 2.075413814, 2.140688197, 2.210452351, 2.28523318, 2.365642792, 2.452396478, 2.546335439, 2.648455802, 2.75994605, 2.882235846, 3.01706052, 3.166547428, 3.333333333, 3.520726642, 3.732935875, 3.97539819, 4.255263139, 4.582124498, 4.96916252, 5.434992778, 6.006790189, 6.72584757, 7.658112588, 8.915817681, 10.70672711, 13.46326037, 18.25863694, 28.69242032, 68.95533643, -158.4943784, -36.21729907, -20.22896451, -13.92536607, -10.55089693, -8.447794056, -7.010715755, -5.965979741, -5.171786508, -4.547320366, -4.043147824, -3.62733258, -3.278323283, -2.981049637, -2.72465641, -2.501126036, -2.304408198, -2.129851283, -1.973820239, -1.833433222, -1.706376086, -1.590769119, -1.485069639, -1.387999671, -1.29849148, -1.21564602, -1.138700863, -1.067005175, -1};
#endif	// not REMOTE_AUTODETECT

#endif


	FlagStatus enable = RESET;
		int16_t pwmSlave = 0;

		uint16_t nicoRxCRC = 0;
		uint16_t nicoCalcCRC = 0;
		
		uint8_t nicoRawData[128];
		uint16_t nicoRawIndex = 0;
	
uint32_t iTimeNextLoop = 0;
//----------------------------------------------------------------------------
// MAIN function
//----------------------------------------------------------------------------
#if defined(PLATFORMIO) && TARGET==22	// no longer neccessary for target 2
	uint32_t SystemCoreClock = 72000000;  // Define the missing symbol
#endif

int main (void)
{
	iBug = 1;
	ConfigRead();		// reads oConfig defined in defines.h from flash
	
	Clock_init();		// GD32F103 allows for 72MHz, STM32F103 only for 64 MHz internal clock
	SysTick_Config(SystemCoreClock / 1000);	//  Configure SysTick to generate an interrupt every millisecond
	//Clock_test();		// 72Mhz: iTestClock=12000, 64Mhz=13500, 48Mhz=18000 = 18 seconds fron power on to startup melody. 124Mhz = 7000
						// PlatformIO binary: 72 Mhz=11000=11seconds, 64MHz=12380, 124Mhz=6388=6.4s . Better assembler code ?
		
	#ifdef MASTER_OR_SINGLE
		FlagStatus chargeStateLowActive = SET;
		int16_t pwmMaster = 0;
		int16_t scaledSpeed = 0;
		int16_t scaledSteer  = 0;
		float expo = 0;
		float steerAngle = 0;
		float xScale = 0;
	#endif
	
		
	if (	Watchdog_init() == ERROR)	// Init watchdog
		while(1);	// If an error accours with watchdog initialization do not start device
	
	// Init Interrupts
	Interrupt_init();

	#if TARGET != 3	// did not work for gd32e230 :-/
		// Init timeout timer
		TimeoutTimer_init();
	#endif

	// Init GPIOs
	GPIO_init();
	
	#ifndef REMOTE_AUTODETECT
		DEBUG_LedSet(SET,0)
		//pinMode(LED_GREEN,	GPIO_MODE_IPU);		// input_pullup turns led on with target 2
		//digitalWrite(LED_GREEN,0);	// not working for taget 2
	
		#ifdef UPPER_LED
			digitalWrite(UPPER_LED,SET);
		#endif

		#ifdef SELF_HOLD
			// Activate self hold direct after GPIO-init
			digitalWrite(SELF_HOLD,SET);
		#endif
	#endif

	#ifdef USART0_BAUD
			USART0_Init(USART0_BAUD);
	#endif
	#ifdef USART1_BAUD
			USART1_Init(USART1_BAUD);
	#endif
	#ifdef USART2_BAUD
			USART2_Init(USART2_BAUD);
	#endif

	#ifdef I2C_ENABLE
		I2C_Init();
		uint8_t iAddr = i2c_scanner();
		if (iAddr>0)	dump_i2c_registers(iAddr);		// 0x68
	#endif 

	#ifdef IMU_ENABLE
		MPU_Init();
	#endif

	// Init ADC
	ADC_init();

	// Init PWM
	PWM_init();

	InitBldc();		// virtual function implemented by bldcBC.c and bldcSINE.c
	DriverInit(iDrivingMode);



/*
	// added by deepseek: Apply fixed PWM pattern to lock rotor to known position
	does heavily freeze the motor :-(
	timer_channel_output_pulse_value_config(TIMER_BLDC, TIMER_BLDC_CHANNEL_G, BLDC_TIMER_MID_VALUE);
	timer_channel_output_pulse_value_config(TIMER_BLDC, TIMER_BLDC_CHANNEL_B, BLDC_TIMER_MID_VALUE);
	timer_channel_output_pulse_value_config(TIMER_BLDC, TIMER_BLDC_CHANNEL_Y, 0);
	uint32_t iTimeWait = millis() + 500;
	while (millis()<iTimeWait){	fwdgt_counter_reload();};
*/
	
	// Device has 1,6 seconds to do all the initialization
	// afterwards watchdog will be fired
	//while(1)
	fwdgt_counter_reload();

#ifdef REMOTE_AUTODETECT
  while(1)
	{
		if (millis() < iTimeNextLoop)	
			continue;
		iTimeNextLoop = millis() + DELAY_IN_MAIN_LOOP;
		
		steerCounter++;		// something like DELAY_IN_MAIN_LOOP = 5 ms
		
		if ((steerCounter % 2) == 0)	// something like DELAY_IN_MAIN_LOOP = 10 ms
		{
			RemoteUpdate();
		}
		SetEnable(1);

		// Reload watchdog (watchdog fires after 1,6 seconds)
		fwdgt_counter_reload();
	}
}

#else	

	// Startup-Sound
	BUZZER_MelodyDown()
	#ifdef BUTTON
		// Wait until button is released
		
		uint32_t iTimePushed = millis();
		while (BUTTON_PUSHED == digitalRead(BUTTON))
		{
			fwdgt_counter_reload();	// Reload watchdog while button is pressed
			#ifdef REMOTE_ADC
				if (millis()-iTimePushed > 2000)
				{
					iConfigMode = 1;
					BuzzerSet(8,2);	// (iFrequency, iPattern)
				}
			#endif
		} 
		Delay(10); //debounce to prevent immediate ShutOff (100 is to much with a switch instead of a push button)
	#endif

	DEBUG_LedSet(RESET,0)
	//pinMode(LED_GREEN,	GPIO_MODE_OUT_PP);	//turns off led on target 2
	//digitalWrite(LED_GREEN,1);	// not working for target 2

	#ifdef UPPER_LED
		digitalWrite(UPPER_LED,RESET);
	#endif
iBug = 10;

	while(1)
	{
		if (millis() < iTimeNextLoop)	
			continue;
		iTimeNextLoop = millis() + DELAY_IN_MAIN_LOOP;
		steerCounter++;		// something like DELAY_IN_MAIN_LOOP = 5 ms
		DEBUG_LedSet(	(steerCounter%20) < 10	,0)
		//DEBUG_LedSet(	digitalRead(BUTTON)	,1)		
		//iBug = digitalRead(BUTTON);
		
		
		#ifdef MOSFET_OUT
			digitalWrite(MOSFET_OUT,	(steerCounter%200) < 100	);	// onboard led blinking :-)
		#endif
		
		#ifdef SLAVE	
			SetBldcInput(pwmSlave);
		#else	//MASTER_OR_SINGLE
			if ((steerCounter % 2) == 0)	// something like DELAY_IN_MAIN_LOOP = 10 ms
			{
				#if defined(PILOT_DEFAULT) && defined(SEND_IMU_DATA)
					if (MPU_ReadAll() != SUCCESS) 
					{
						I2C_Init();	// try to re-init if i2c bus fails. Need when I2C_SPEED is 400000 instead of 200000
						//MPU_Init();		// re-init mpu6050 (not really needed)
						iBug++;
					}
				#endif
				
				RemoteUpdate();
				//DEBUG_LedSet(RESET,0)
			}
/*
			if ((steerCounter % 1000) == 0)
			{
				uint8_t iAddr = i2c_scanner();
				if (iAddr>0)	dump_i2c_registers(iAddr);
			}
*/			
			if (speedShutoff)	speed = ShutOff();
			
			#ifdef PILOT_DEFAULT
				if (iDrivingMode == 0)
				{
					// Calculate expo rate for less steering with higher speeds
					expo = MAP((float)ABS(speed), 0, 1000, 1, 0.5);
					
					// Each speedvalue or steervalue between 50 and -50 (STAND_STILL_THRESHOLD) means absolutely no pwm
					// -> to get the device calm 'around zero speed'
					scaledSpeed = speed < STAND_STILL_THRESHOLD && speed > -STAND_STILL_THRESHOLD ? 0 : CLAMP(speed, -speedLimit, speedLimit) * SPEED_COEFFICIENT;
					scaledSteer = steer < STAND_STILL_THRESHOLD && steer > -STAND_STILL_THRESHOLD ? 0 : CLAMP(steer, -speedLimit, speedLimit) * STEER_COEFFICIENT * expo;
					
					// Map to an angle of 180 degress to 0 degrees for array access (means angle -90 to 90 degrees)
					steerAngle = MAP((float)scaledSteer, -1000, 1000, 180, 0);
					xScale = lookUpTableAngle[(uint16_t)steerAngle];

					// Mix steering and speed value for right and left speed
					if(steerAngle >= 90)
					{
						pwmSlave = CLAMP(scaledSpeed, -1000, 1000);
						pwmMaster = CLAMP(pwmSlave / xScale, -1000, 1000);
					}
					else
					{
						pwmMaster = CLAMP(scaledSpeed, -1000, 1000);
						pwmSlave = CLAMP(xScale * pwmMaster, -1000, 1000);
					}
				}
				else
				{
					// simply boost/drop speed left and right according to steer going from -1.0 to +1.0
					pwmMaster = speed * (1+steer/1000.0);		
					pwmSlave = speed * (1-steer/1000.0);
				}
			#else
				Pilot(&pwmMaster,&pwmSlave);
			#endif
			
					// Set output
			SetBldcInput(pwmMaster);

			#ifdef USART_MASTERSLAVE
				// Decide if slave will be enabled
				if  ((enable == SET && timedOut == RESET))
					wStateSlave = wStateSlave & !STATE_Disable;
				else
					wStateSlave |= STATE_Disable;

				#ifdef MASTER
					SendSlave(-pwmSlave);
				#endif

			#endif

			if (batteryVoltage > BAT_LOW_LVL1)	// Show green battery symbol when battery level BAT_LOW_LVL1 is reached
			{
				ShowBatteryState(0);
				#ifdef BEEP_BACKWARDS
				if (beepsBackwards == SET && speed < -50)
					{
						BuzzerSet(5,4)	// (iFrequency, iPattern)
					}
					else
				#endif
				{
					BuzzerSet(0,0)	// (iFrequency, iPattern)
				}
			}
			else if (batteryVoltage > BAT_LOW_LVL2) // Make silent sound and show orange battery symbol when battery level BAT_LOW_LVL2 is reached
			{
				ShowBatteryState(1);
				#ifdef BATTERY_LOW_BEEP
					BuzzerSet(6,3)	// (iFrequency, iPattern)
				#endif
			}
			else if  (batteryVoltage > BAT_LOW_DEAD) // Make even more sound and show red battery symbol when battery level BAT_LOW_DEAD is reached
			{
				ShowBatteryState(2);
				#ifdef BATTERY_LOW_BEEP
					BuzzerSet(6,2)	// (iFrequency, iPattern)
				#endif
			}
			else 	// Shut device off, when battery is dead
			{
				ShowBatteryState(3);
				#ifdef BATTERY_LOW_BEEP
					BuzzerSet(6,1)	// (iFrequency, iPattern)
				#endif
				#ifdef BATTERY_LOW_SHUTOFF
					ShutOff();
				#endif
			}

			#ifdef BUTTON
				// Shut device off when button is pressed
				if (BUTTON_PUSHED == digitalRead(BUTTON))
				//if (gpio_input_bit_get(BUTTON_PORT, BUTTON_PIN))
				{
					while (BUTTON_PUSHED == digitalRead(BUTTON)) {fwdgt_counter_reload();}
					//while (gpio_input_bit_get(BUTTON_PORT, BUTTON_PIN)) {fwdgt_counter_reload();}
					ShutOff();
				}
			#endif
			
			// Calculate inactivity timeout (Except, when charger is active -> keep device running)
			if (ABS(pwmMaster) > 50 || ABS(pwmSlave) > 50 || !chargeStateLowActive)
			{
				inactivity_timeout_counter = 0;
			}
			else
			{
				inactivity_timeout_counter++;
			}
			
			#ifdef INACTIVITY_TIMEOUT
				// Shut off device after INACTIVITY_TIMEOUT in minutes
				if (inactivity_timeout_counter > (INACTIVITY_TIMEOUT * 60 * 1000) / (DELAY_IN_MAIN_LOOP + 1))
				{ 
					ShutOff();
				}
			#endif
		#endif	

		#if defined(CHARGE_STATE) && defined(MASTER_OR_SINGLE)
			chargeStateLowActive = digitalRead(CHARGE_STATE);
			enable = chargeStateLowActive;
		#else
			enable = SET;			
		#endif
		
		if (bPilotTimeout || bRemoteTimeout || (wState & STATE_Disable))	enable = RESET;
		
		// Enable is depending on arm switch
		//#ifdef USART_CRSF
		//enable &= (getChannel(4)-1024) > 0; //arm switch doesn't work
		//#endif
		//enable = SET;		// robo testing
		//^enable = RESET;
		
		//DEBUG_LedSet(enable,0);	// macro. iCol: 0=green, 1=organge, 2=red
			
		// Enable channel output
		SetEnable(enable);

		//wState = STATE_LedBattLevel;	// overwrite wState recevied from RemoteUart or RemoteUartBus
		
		#if (!defined(TEST_HALL2LED)) && (!defined(DEBUG_LED))
			if (!(wState & STATE_LedBattLevel))
			{
				#ifdef LED_GREEN
					digitalWrite(LED_GREEN,wState & STATE_LedGreen ? SET : RESET);
				#endif
				#ifdef LED_ORANGE
					digitalWrite(LED_ORANGE,wState & STATE_LedOrange ? SET : RESET);
				#endif
				#ifdef LED_RED
					digitalWrite(LED_RED,wState & STATE_LedRed ? SET : RESET);
				#endif
			}
		#endif
		#ifdef UPPER_LED
			digitalWrite(UPPER_LED,wState & STATE_LedUp ? SET : RESET);
		#endif
		#ifdef UPPER_LED
			digitalWrite(UPPER_LED,wState & STATE_LedDown ? SET : RESET);
		#endif

		if (wState & STATE_Shutoff)	ShutOff();


		//Delay(DELAY_IN_MAIN_LOOP);
		
		fwdgt_counter_reload(); // Reload watchdog until device is off
  }
}

//----------------------------------------------------------------------------
// Turns the device off
//----------------------------------------------------------------------------

int32_t ShutOff(void)
{
	
	if (speedShutoff)
	{
		speedShutoff += speedShutoff > 0 ? -5 : +5 ;
		if (ABS(speedShutoff) > 10)
			return speedShutoff;
	}
	else if (ABS(speed)>10)
	{
		speedShutoff = speed;
		return speedShutoff;
	}
	
	BUZZER_MelodyUp()
	
	#ifdef USART_MASTERSLAVE
	
		#ifdef MASTER
			// Send shut off command to slave
			wStateSlave = STATE_Shutoff;
			SendSlave(0);
		#endif

	// Disable usart
		usart_deinit(USART_MASTERSLAVE);
	#endif
	
	// Set pwm and enable to off
	SetEnable(RESET);
	iDrivingMode = 0;
	SetBldcInput(0);
	
	#ifdef SELF_HOLD
		digitalWrite(SELF_HOLD,RESET);
	#endif
	while(1)	fwdgt_counter_reload(); // Reload watchdog until device is off
}


#ifdef MASTER_OR_SINGLE

//----------------------------------------------------------------------------
// Shows the battery state on the LEDs
//----------------------------------------------------------------------------
void ShowBatteryState(int8_t iLevel)
{
	#ifdef DEBUG_LED
		return;
	#else
		if (!(wState & STATE_LedBattLevel))
			return;
		uint32_t aPin[3];
		uint8_t iLedCount=0;
		#if defined(LED_GREEN)
			aPin[iLedCount++] = LED_GREEN;
		#endif
		#if defined(LED_ORANGE)
			aPin[iLedCount++] = LED_ORANGE;
		#endif
		#if defined(LED_RED)
			aPin[iLedCount++] = LED_RED;
		#endif

		if (iLedCount == 3)		// green -> orange -> red -> blinking red
		{
			int8_t i=2; 
			if (iLevel == 3)
			{
				digitalWrite(aPin[2],(steerCounter%50) < 25);		// red led blinking
				i--;
			}
			for(;i>=0;i--)
			{
				digitalWrite(aPin[i],i==iLevel);
			}
			
		}
		else if (iLedCount == 2)	// show the level 0-3 in 2 bits
		{
			digitalWrite(aPin[0],iLevel & 0b01);		
			digitalWrite(aPin[1],iLevel & 0b10);		
		}
		else if (iLedCount == 1)
		{
			if (iLevel == 0) 		
				digitalWrite(aPin[0],1);		
			else
			{
				uint16_t iPeriod = 300/(2*iLevel);
				digitalWrite(aPin[0],(steerCounter%iPeriod) < (iPeriod/2)	);		// led blinking
			}
		}
	#endif
}

#endif


#endif

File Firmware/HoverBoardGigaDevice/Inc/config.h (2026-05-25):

#ifndef CONFIG_H
#define CONFIG_H

// REMOTE_AUTODETECT
				// ONLY test with 1-2A constant current power supply !!!! The charger with 1.5A might also do :-)
				// will drive the motor without hall input to detect the hall pins..

#ifdef REMOTE_AUTODETECT
	#define WINDOWS_RN		// adds a \r before every \n
	
	//#define RTT_REMOTE

	#define REMOTE_USART				1 	// 	1 is usually PA2/PA3 and the original master-slave 4pin header
																	//	0 is usually PB6/PB7 and the empty header close to the flash-header
																	//	2 is usually PB10/PB11 on stm32f103 boards
																	
#else

	// choose your target in the dropdown list to the top-right of the Keil IDE
	// and then set your layout below
	// Gen2-target-layout is included in defines.h
	#ifdef GD32F130		// TARGET = 1
		#define LAYOUT 9 // 9 Means 2.1.9
		//#define LAYOUT_SUB 19	// Layout 9 means x.x.9?
	#elif GD32F103		// TARGET = 2
		#define LAYOUT 1
		//#define STM32F103 	// uncomment if your board has stm32f103 instead of gd32f103. Will give the max 64 Mhz for STM32
			// Warning: will overclock gd32f103 mcu to 124 MHz and doubling current consumption. Keep GD32 to its 72 Mhz.
	#elif GD32E230		// TARGET = 3
		#define LAYOUT 1
	#elif MM32SPIN05	// TARGET = 4
		#define LAYOUT 1
	#endif

	#define BLDC_BC			// old block commutation bldc control
	//#define BLDC_SINE			// silent sine-pwm motor control, added 2025 by Robo Durden. 
	//#define BLDC_SINE_BOOSTER		// can boost speed by 15% starting from 87% throttle.
	
	#define DRIVING_MODE 0	//  0=pwm, 1=speed in revs/s*1024, 2=torque in NewtonMeter*1024, 3=iOdometer

	//#define SPEED_AsRevsPerSec		// Will overflow at 327 revs/s = 19620 rpm. Hoverboard motor: 14 rpm/V * 50V = 700 rpm

	#define BAT_CELLS         	4        // battery number of cells. Normal Hoverboard battery: 10s
	//#define BATTERY_LOW_SHUTOFF		// will shut off the board below BAT_LOW_DEAD = BAT_CELLS * CELL_LOW_DEAD, 
	//#define BATTERY_LOW_BEEP		// will start beeping for different battery low lwevels

	//#define BEEP_BACKWARDS

	//#define DEBUG_LED		// uncomment to activate DEBUG_LedSet(bSet,iColor) macro. iCol: 0=green, 1=organge, 2=red


	//#define MASTER		// uncomment for MASTER firmware.
	//#define SLAVE			// uncomment for SLAVE firmware.
	#define SINGLE			// uncomment if firmware is for single board and no master-slave dual board setup

	#if defined(MASTER) || defined(SINGLE)
		
		// choose only one 'remote' to control the motor
		//#define REMOTE_DUMMY
				#ifdef REMOTE_DUMMY
					#define REMOTE_PERIOD 3 // 3 = 3 seconds period of the zigzag curve
					#define TEST_HALL2LED	// led the 3-led panel blink according to the hall sensors
					#define RTT_REMOTE	// log and set via ST-Link dongle
						#define WINDOWS_RN		// adds a \r before every \n to RTT log
				#endif
		
		//#define REMOTE_USART 1
		//#define TEST_HALL2LED
		#define DISABLE_CHARGESTATE
				
		//#define REMOTE_UART
		#define REMOTE_UARTBUS	// ESP32 as master and multiple boards as multiple slaves ESP.tx-Hovers.rx and ESP.rx-Hovers.tx
				#ifdef REMOTE_UARTBUS
					//#define TEST_HALL2LED
					#define SLAVE_ID	1		// must be unique for all hoverboards connected to the bus
				#endif
		//#define REMOTE_CRSF		// https://github.com/RoboDurden/Hoverboard-Firmware-Hack-Gen2.x/issues/26
		//#define REMOTE_ROS2		// https://github.com/RoboDurden/Hoverboard-Firmware-Hack-Gen2.x/issues/122
		//#define REMOTE_ADC	// speed is PA2=TX and steer is PA3=RX of the masterslave header. Get 3.3V from the flash header
												// DO NOT use the 5V/15V pin of the masterslave header for the potentiometers !!!!!!!!!
												// SLAVE board has to be connected to the additional UART header, but 5V/15V coming from the masters masterslave header
												// for calibration, hold the on/off button until the startup melody restarts.
												// Then release the button and leave the joystick (the two potentiometers) in neutral position.
												// When the melody returns for 2 seconds, push speed to max.
												// After another 5 seconds + 2 seconds melody: push speed to min. Then steer to max. Finally steer to min
		//#define REMOTE_OPTIMIZEPID		// will zigzag motor and optimize pid parameters for 1=speed or 3=iOdometer.
		// monitor with StmStudio/McuViewer or via ST-Link usb dongle RTT and openocd_rtt_32f1x.bat or PlatformIO RTT_Task
				#ifdef REMOTE_OPTIMIZEPID
					#define WINDOWS_RN		// adds a \r before every \n		
				#endif


		//#define TEST_HALL2LED	// led the 3-led panel blink according to the hall sensors

		//#define RTT_REMOTE		// uncoment for i2c_scanner and dump_i2c_registers to print to rtt :-)
			// needs either I2C_PB8PB9 or I2C_PB6PB7 and MPU_6050 or MPU_6050old or BMI_160 in your defines_2-x-y.h file
		//#define SEND_IMU_DATA // send the IMU data with RemoteUart or RemoteUartBus. Tested for 2.1.20 !
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

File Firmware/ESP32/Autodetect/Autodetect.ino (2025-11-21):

//#define ESP32       // comment out if using Arduino

//#define _DEBUG  // uncomment to get additional debug output
#ifdef _DEBUG
  #define OUTC(code) {code}
  #define OUT(s)  {Serial.print(s);}
  #define OUT2T(s,i)  {Serial.print(s);Serial.print(": ");Serial.print(i);Serial.print("  ");}
  #define OUT2TX(s,i)  {Serial.print(s);Serial.print(": ");Serial.print(i,HEX);Serial.print("  ");}
  #define OUT2N(s,i)  {Serial.print(s);Serial.print(": ");Serial.print(i);Serial.println();}
#else
  #define OUTC(code)
  #define OUT(s)
  #define OUT2T(s,i)
  #define OUT2TX(s,i)
  #define OUT2N(s,i)
#endif

// Serial interface, baud, RX GPIO, TX GPIO
// Note: The GPIO numbers will not necessarily correspond to the
// pin number printed on the PCB. Refer to your ESP32 documentation for pin to GPIO mappings.
#define BAUDRATE 19200   // 19200 is default on hoverboard side because Arudino Nano SoftwareSerial can not do 115200

// ------- BOARD-SPECIFIC SERIAL SETUP --------
#if defined(ARDUINO_ARCH_ESP8266)

// ESP8266: use SoftwareSerial for hoverboard
#include <SoftwareSerial.h>
const int pinRX = D5, pinTX = D6;   // pick whatever pins you actually wired
SoftwareSerial oSerialHover(pinRX, pinTX); // RX, TX

#elif defined(ESP32)

// Original ESP32 block (unchanged)
const int pinRX = 12, pinTX = 14;
#define oSerialHover Serial1    // ESP32

#else

// Original "Arduino" block (unchanged)
#include <SoftwareSerial.h>    
const int pinRX = 9, pinTX = 8;
SoftwareSerial oSerialHover(pinRX,pinTX); // RX, TX 
#define oSerialHover Serial    // Arduino

#endif
// --------------------------------------------

void setup() 
{
  pinMode(LED_BUILTIN, OUTPUT);
  Serial.begin(115200);
  Serial.println("Hello Hoverbaord V2.x Autodetect :-)");

  // ------- BOARD-SPECIFIC begin() CALL -------
  #if defined(ARDUINO_ARCH_ESP8266)

    // ESP8266 SoftwareSerial: only needs baud rate
    oSerialHover.begin(BAUDRATE);

  #elif defined(ESP32)

    // Original ESP32 call (unchanged)
    oSerialHover.begin(BAUDRATE, SERIAL_8N1, pinRX, pinTX);

  #else

    // Original "Arduino" call (unchanged)
    oSerialHover.begin(iBaud);

  #endif
  // -------------------------------------------
}

#define PINS_DETECT 18
const char* asScan[PINS_DETECT] = {"HALL_A","HALL_B","HALL_C","PHASE_A","PHASE_B","PHASE_C","LED_RED","LED_ORANGE","LED_GREEN","UPPER_LED","LOWER_LED","ONBOARD_LED","BUZZER","VBATT","CURRENT_DC","SELF_HOLD","BUTTON","BUTTON_PU"};
uint32_t aiPinScan[PINS_DETECT] = {0,0,0,0,0,0,0,0,0,0,0,0,0,0,0,0,0,0};    // the found pins

typedef struct __attribute__((packed, aligned(1))) {
  uint8_t cStart;   //  = '/';
  uint8_t wCmd;
} HeaderData;

enum{  DATA_None, DATA_Request, DATA_Save};
HeaderData oDataHeader = {0x01,DATA_None};  // wenn autodetect.ino receives 0x01 it stores the incoming data or returns it's storage


unsigned long iTimeTest = 0;
int iSerialHoverType = 0;
void loop() 
{
  digitalWrite(LED_BUILTIN, (millis()%2000) < 500);
  if (Serial.available())  // If anything comes in Serial (USB),
  {      
    char c = Serial.read();
    //Serial.println(c );
    oSerialHover.write(c);   // read it and send it to hoverboard
  }

  if (oSerialHover.available())   // If anything comes in from hoverboard
  {     
    if (iSerialHoverType==1)
    {
      int iAvail = oSerialHover.available();
      //OUT2T("iAvail",iAvail)
      if (iAvail < sizeof(HeaderData)-1 +sizeof(aiPinScan))
        return;

      HeaderData oHeaderRx;
      uint32_t aiPinScanRx[PINS_DETECT];
      oSerialHover.readBytes(((uint8_t*)&oHeaderRx)+1, sizeof(oDataHeader)-1);   // 0x01 already read
      oSerialHover.readBytes((uint8_t*)aiPinScanRx, sizeof(aiPinScanRx));
      iSerialHoverType = 0;
        
      OUT2N(oHeaderRx.wCmd,oDataHeader.wCmd)
      if (oHeaderRx.wCmd == DATA_Request)
      {
        oSerialHover.write((uint8_t*) &oDataHeader, sizeof(oDataHeader)); 
        //delay(100);
        oSerialHover.write((uint8_t*) aiPinScan, sizeof(aiPinScan)); 
        OUT2N("DATA_Request",sizeof(oDataHeader)+sizeof(aiPinScan));
      }
      else
      {
        oDataHeader.wCmd = oHeaderRx.wCmd;  // store for later request
        memcpy((uint8_t*)aiPinScan, (uint8_t*)aiPinScanRx, sizeof(aiPinScanRx));
      }
      OUTC(
        #define AHB2_BUS_BASE         ((uint32_t)0x48000000U)        /*!< ahb2 base address                */

        OUT("\npins:\t")
        for (int i=0; i<PINS_DETECT; i++)
        {  
          OUT2T(asScan[i],aiPinScan[i] & ~AHB2_BUS_BASE)
        }
        OUT("\n")
      )
      return;    
    }

    char c = oSerialHover.read();

    // MM32 pinFinder: emulate serial bridge
    if (  (c >= 0x11) && (c <= 0x14)  )
    {
      oSerialHover.write(c);  // send back to hoverboard because MM32 pinFinder that way detects your serial port :-)
      return;
    }
    else if (c == 0x01)  // GD32 autodetect temporary storage
    {
      iSerialHoverType = 1;
      return;
    }
    Serial.write(c);   // read it and send it out Serial (USB)
  }
  if (iTimeTest > millis())
    return;
  iTimeTest = millis() + 1000;
  //Serial.println(millis()); 
}

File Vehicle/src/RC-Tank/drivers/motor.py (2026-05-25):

import time
import struct
import serial  # type: ignore
import threading
from core.types import MotorCommand
from core.config import get_logger

motor = get_logger("motor")

BLACK = "\033[0;30m"
RED = "\033[0;31m"
GREEN = "\033[0;32m"
BROWN = "\033[0;33m"
BLUE = "\033[0;34m"
PURPLE = "\033[0;35m"
RESET = "\033[0m"

class Motor:
    def __init__(self,
                 port: str = "/dev/ttyTHS1",
                 baudrate: int = 4800,
                 send_interval: float = 0.1,
                 max_speed: int = 1000):
       
        self.PORT = port
        self.BAUDRATE = baudrate
        self.SEND_INTERVAL = send_interval # in s
        self.MAX_SPEED = max_speed

        self.ser = serial.Serial(self.PORT, baudrate=self.BAUDRATE, timeout=1)
        self.ser.reset_input_buffer()
        self.ser.reset_output_buffer()

        self._state_lock = threading.Lock()
        self.last_update_time = time.time()
        self.desired_left = 0
        self.desired_right = 0
        self.applied_left = 0
        self.applied_right = 0

        self.voltage: float = 0.0

        self.stopped = True

        self._stop_event = threading.Event()
        self._io_thread = threading.Thread(target=self._io_worker, daemon=True)
        self._io_thread.start()
    
    def stop(self):
        """Request the I/O loop to exit and wait for shutdown."""
        self._stop_event.set()
        if self._io_thread.is_alive():
            self._io_thread.join(timeout=2)
    
    def calc_crc(self, data: bytes) -> int:
        crc = 0
        for byte in data:
            crc ^= (byte << 8)
            for _ in range(8):
                if crc & 0x8000:
                    crc = (crc << 1) ^ 0x1021
                else:
                    crc <<= 1
        return crc & 0xFFFF  # Ensure a 16-bit CRC

    def read_feedback(self):
        try:
            waiting = self.ser.in_waiting
            if waiting > 0:
                data = self.ser.read(waiting)
                if data:
                    motor.debug(f"Received: {data.hex()}")
                    return data
        except serial.SerialException as exc:
            motor.error(f"{RED}Serial read failed: {exc}{RESET}")
            raise
        return None

    def read_voltage_from_uart(self, data):
        """
        Read battery voltage from hoverboard UART data.  
        
        Args: 
            data: bytes or bytearray from UART
            
        Returns:  
            float: Voltage in volts, or None if no valid packet found
        """
        # Handle None or empty data
        if data is None or len(data) == 0:
            return None
        
        # Convert to bytearray if needed
        if isinstance(data, str):
            # If hex string like "cdab01ae11f605..."
            data = bytes.fromhex(data. replace('\\x', ''))
        elif isinstance(data, bytes):
            data = bytearray(data)
        
        # Need at least 15 bytes for a complete packet
        if len(data) < 15:
            return None
        
        # Find start frame (CD AB)
        for i in range(len(data) - 14):  # Need at least 15 bytes
            if data[i] == 0xCD and data[i+1] == 0xAB:
                # Found start frame, extract voltage at bytes 5-6
                volt_lo = data[i + 5]
                volt_hi = data[i + 6]
                
                # Combine (little-endian)
                voltage_raw = (volt_hi << 8) | volt_lo
                
                # Convert to volts
                voltage = voltage_raw / 100.0
                
                return voltage
        
        return None  # No valid packet found

    
    def build_packet(self, iSlave: int, iSpeed: int, wState: int) -> bytes:
        """
        Build UART packet in `SerialServer2Hover` format:
        Start Byte (1B) + Data Type (1B) + Slave ID (1B) + Speed (2B LE) + State (1B) + CRC (2B LE)
        """
        START_BYTE = b'\x2F'  # Start byte, `/` in ASCII
        DATA_TYPE = b'\x00'  # Data type (`0x00` for SerialServer2Hover)
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

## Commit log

2025-10-17 Update CAD readme
2025-10-17 Add cad files
    [Platform_Riser.3mf, Platform_Riser.f3d]
2025-10-17 Add new photos and CAD
    [Platform_Riser_V2.3mf, Platform_Riser_V2.f3d]
2025-10-17 Add new pictures
    [Platform_Riser_V3.3mf, Platform_Riser_V3.f3d]
2025-10-18 Add ESC PWM test script
2025-10-18 Add code for right motor
2025-10-18 Flip pwm pins
2025-10-18 Add camera code
2025-10-19 Add 90 clockwise because of new cam mount
2025-10-19 Add timeout debug print statements
2025-10-21 WIP: Add cam switch
2025-10-22 WIP: Make switch look nicer
2025-10-30 Add no camera icon
2025-11-01 Switch from asyncio to threading
2025-11-01 Add timeout hit print
2025-11-01 WIP: Add car steering
2025-11-01 Add car steering
2025-11-01 Add car mode switch
2025-11-01 WIP: Fix camera size
    [streamerClass.py]
2025-11-05 WIP: Start adding WebRTC; fastrtc needs fastapi, so switching from flask to that
2025-11-26 Add test code for new motors
2025-11-26 Update to use remote uart bus
2025-11-26 Make new firmware for uart bus
2025-11-28 Turn off steer
2025-11-29 Remove old motor cmds from api for testing
2025-11-29 Rewrite motor_class.py for new esc's
2025-11-29 Add camera
2025-11-30 Fix MJPEG streaming latency and add graceful shutdown handling
    [streamerClass.py]
2025-12-21 Add debug to camera class
2025-12-21 Flip motors to go right way
2025-12-22 Read battery voltage
2025-12-22 Fix voltage stuff
2025-12-22 Add light switching code
2026-02-28 Add fan stuff
2026-03-10 Fix camera number
2026-03-14 Remove fan junk
2026-03-14 Change motor uart
2026-03-14 Fix motor UART
2026-03-14 Switch to video 0
2026-03-14 Jetson SPI
2026-03-15 CORRECT PORT FOR ONCE
    [gps_config_rtk.py]
2026-03-29 Change I2C bus
2026-03-29 Change device ID
2026-03-29 Change to print statement
2026-04-22 Move Firmware to root
    [100ask-openjtag.cfg, 8devices-lima.cfg, actux3.cfg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]
2026-04-24 Update set motor
2026-04-24 Fix motor cmd
2026-04-24 Test new motor layout
2026-04-27 Print offsets
2026-04-27 Don't send motor cmds if not on motor page
2026-04-27 Add code to stop motors aafter self driving
2026-05-02 Remove extra print statement
2026-05-02 Stop motors when switching pages
2026-05-02 Work on motor stop issues
2026-05-02 Test new failsafe settings
    [motor.py]
2026-05-03 Test new mountpoint
2026-05-05 Print fix type
2026-05-05 Print correct fix type
2026-05-05 Don't print user and pass
2026-05-10 Replace GPS library with new, working, RTK version
    [gps.py]
2026-05-17 Add self driving buttons
2026-05-20 Fix button offset on IP screen
2026-05-24 refactor motor serial I/O to single worker thread
    Agent-Logs-Url: https://github.com/niiccoo2/RC-Tank/sessions/a7a0baf9-be16-46a5-aeb8-6c5e99a1472f
2026-05-25 Add keybind for autopilot button
2026-05-25 Add delete all waypoints button
2026-05-25 WIP: Fix ESC issues
    [bldc.c, config.h, motor.py]
2026-05-25 Fix ESC issues
2026-05-26 Add PID debug
2026-05-30 Add pid
2026-05-30 Tune PID
2026-05-30 Read PID from file
2026-05-30 Stop graphing PID data
2026-06-29 Work on frame
    [Chassis_V4_Start_On_Front.f3d]
